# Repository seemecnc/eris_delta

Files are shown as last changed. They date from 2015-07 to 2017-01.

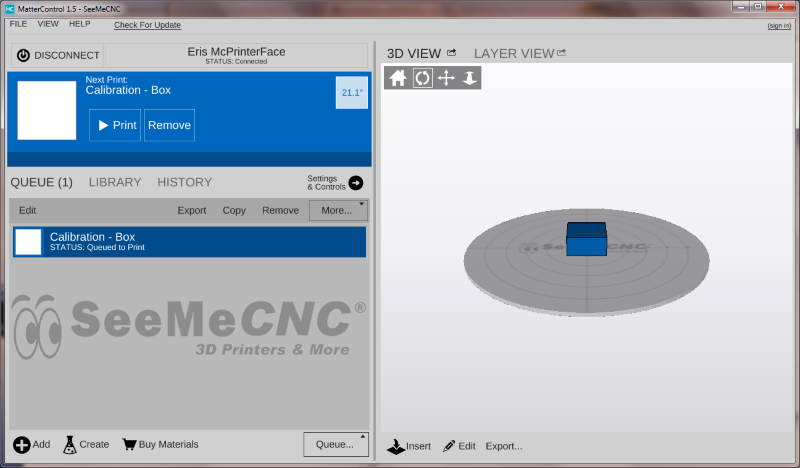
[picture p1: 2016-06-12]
User Guide/Images/mc running.png

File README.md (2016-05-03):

ERIS Delta 3D Printer
=====================

ERIS is an affordable desktop 3D printer built by SeeMeCNC.  We designed this machine to be fast, easy to use and much more affordable than any of our previous designs.  

3/2/16
DIR Repetier-Firmware-092.2-ERIS is workign on prototypes

3/3/16
DIR Repetier-Firmware-092.2-ERIS-ii2dh is modified 092 firmware from UltiMachine for accelerometer probing on new hotend PCB board

####

Case fan goes to fan port 2
Hotend fan goes to fan port 1

Red motor wire to right (opposite of the USB side of mini rabmo)

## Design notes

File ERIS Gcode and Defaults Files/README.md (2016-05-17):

This folder contains default settings files and calibration Gcode files.

ERIS_DEFAULTS.ini is the default slicing settings for MatterControl using
their Matterslice slicing engine

CALIBRATION.txt is the gcode script for calibrating using the accel probe
on the HE280 Hotend

LOAD_FILAMENT.txt is a gcode script to automatically load filament
in an eris delta.  MAKE SURE you only have the filament loaded to where you
can just start to see it coming out of the connector on the EZStruder NOT 
all the way up to the hotend!!!

UNLOAD_FILAMENT.txt is a gcode script to automatically unload filament
in an eris delta

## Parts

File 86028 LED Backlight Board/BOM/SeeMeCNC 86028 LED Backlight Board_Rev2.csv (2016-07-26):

LibRef | Comment | Description | Designator | Footprint | Quantity
ERJ-3EKF1001V | 1K | RES 0603 1K 100mW 1% | R19, R22, R25 | R0603 | 3
ERJ3EKF4701V | 4.7K | RES 0603 4.7K 100mW 1% | R26, R27 | R0603 | 2
GRM155R71C104KA88D | 100nF | CAP CER 0402 100nF 16V 10% X7R | C19 | C0402 | 1
CRCW0805180RJNEA | 180 | Resistor | R1, R2, R3, R4, R5, R6, R18, R21, R24 | R0805 | 9
APT3216VBC/D | APT3216VBC/D | LED BLUE CLEAR 1206 SMD | LED1, LED2, LED3, LED4 | LED1206 | 4
FIDUCIAL | FIDUCIAL | Fiducial | FID1, FID2 | FIDUCIAL-1X2 | 2
Header 4 | Header 4 | Header, 4-Pin | P1, P2 | HDR1X4 | 2
LTST-C19HE1WT | LTST-C19HE1WT | LED RGB DIFFUSED 0606 SMD | LED5 | LTST-C19HE1WT | 1
MMBT3904 | MMBT3904 |  | Q2, Q3, Q4 | SOT23-3 | 3
IC PCA9632 | PCA9632DP2 | IC LED DRIVER RGBA | U3 | IC TSSOP-10 | 1

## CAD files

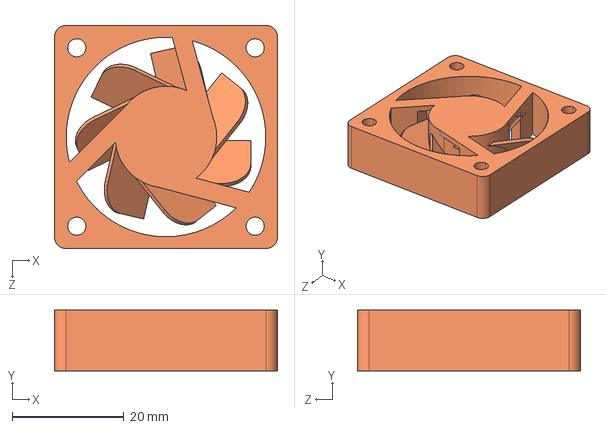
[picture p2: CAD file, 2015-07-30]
ErisRev1 CAD Source/Fan - 40mm X 40mm X 10mmT DC12V-015A - Copy.IGS
40.0 x 10.9 x 40.0 mm

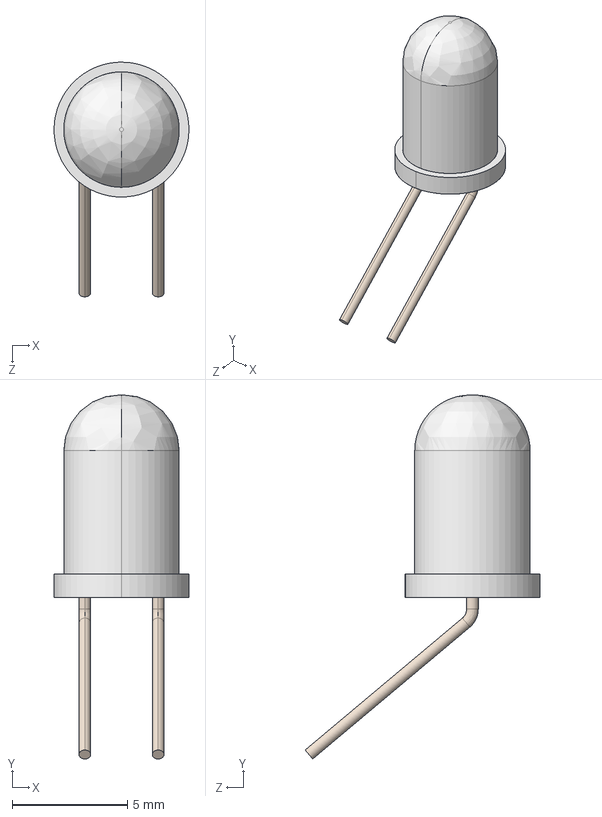
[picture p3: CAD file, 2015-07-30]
ErisRev1 CAD Source/LED - 5mm White.IGS
5.84 x 15.8 x 10.2 mm

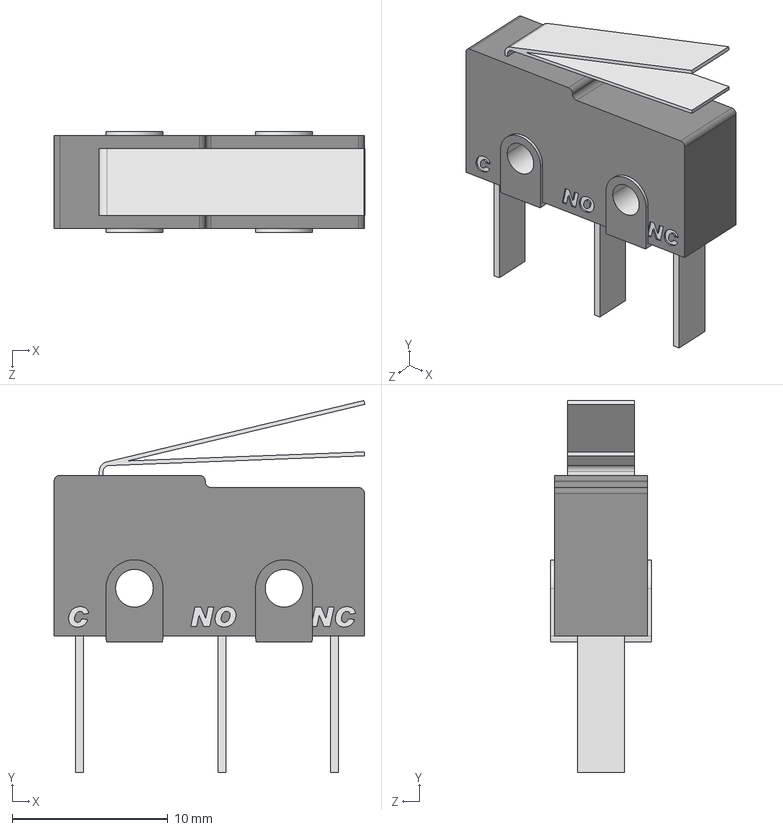
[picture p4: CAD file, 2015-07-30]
ErisRev1 CAD Source/Switch Micro Lever.IGS
19.9 x 23.9 x 6.48 mm

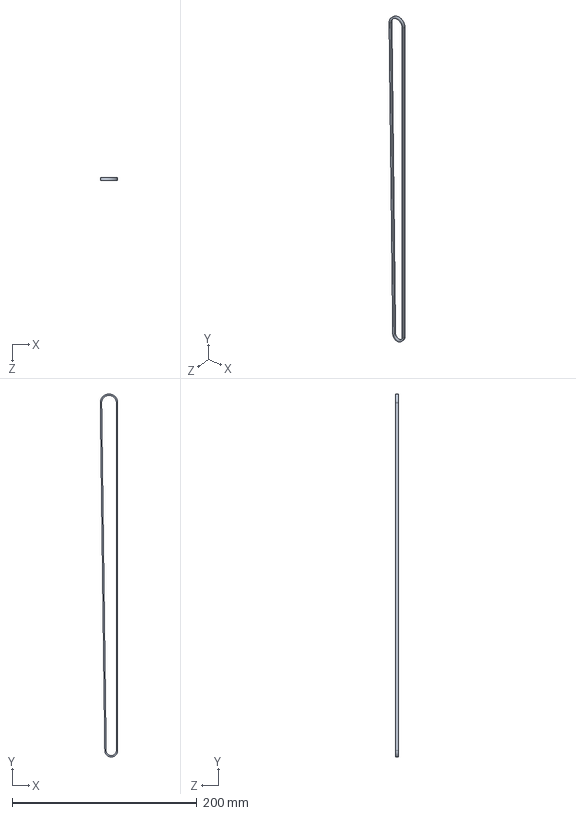
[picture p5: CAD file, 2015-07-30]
ErisRev1 CAD Source/GT2 Timing Belt 3mm.IGS
18.9 x 393.5 x 3.00 mm

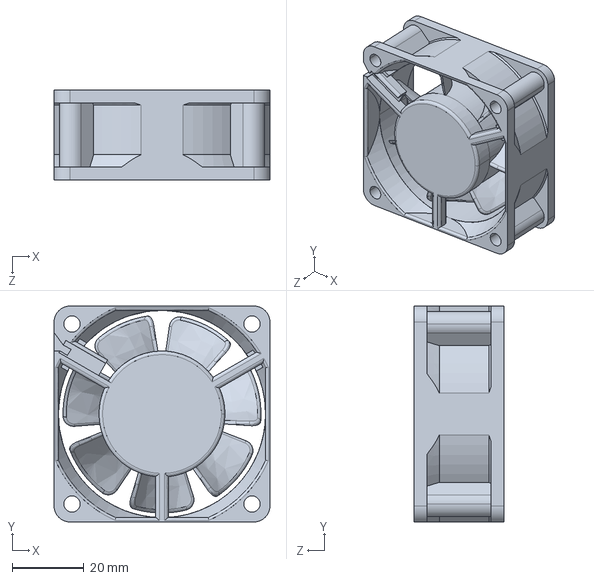
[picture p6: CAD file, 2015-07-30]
ErisRev1 CAD Source/Fan 60mm X 60mm X25mmT DC12V.IGS
60.0 x 60.0 x 25.0 mm

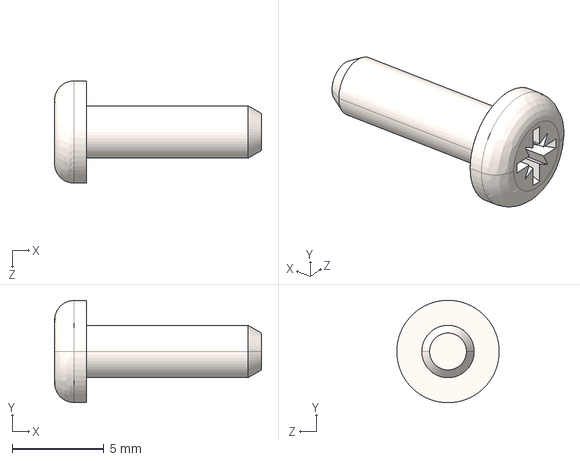
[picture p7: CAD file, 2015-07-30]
ErisRev1 CAD Source/No 4 x 0375L PANHTS SS Sheet Metal PANHTS 0.112-24-type II-B-0.375-N.IGS
11.3 x 5.56 x 5.56 mm

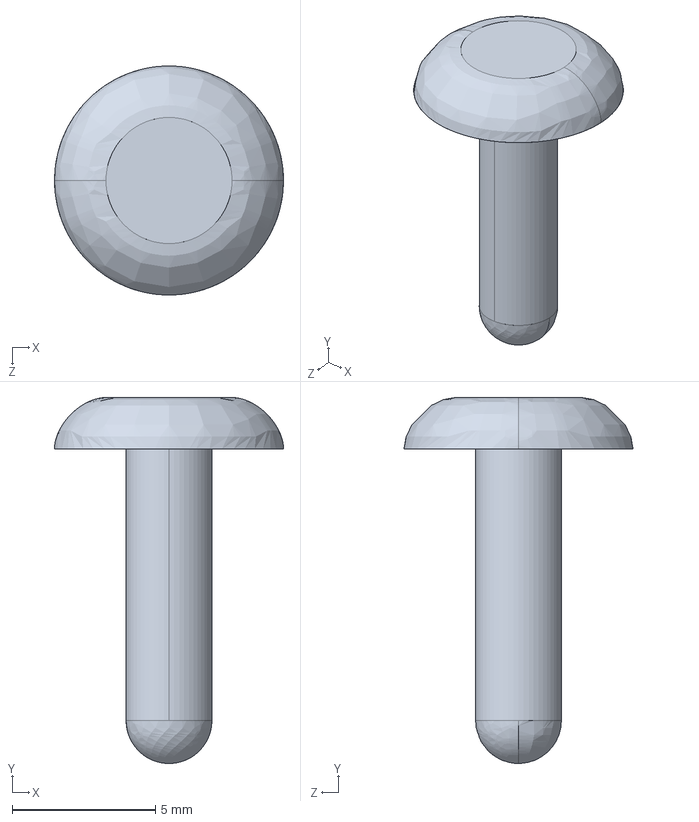
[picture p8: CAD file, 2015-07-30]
ErisRev1 CAD Source/Nylon Click-Lock Shank Rivet_Male.IGS
8.01 x 12.8 x 8.01 mm

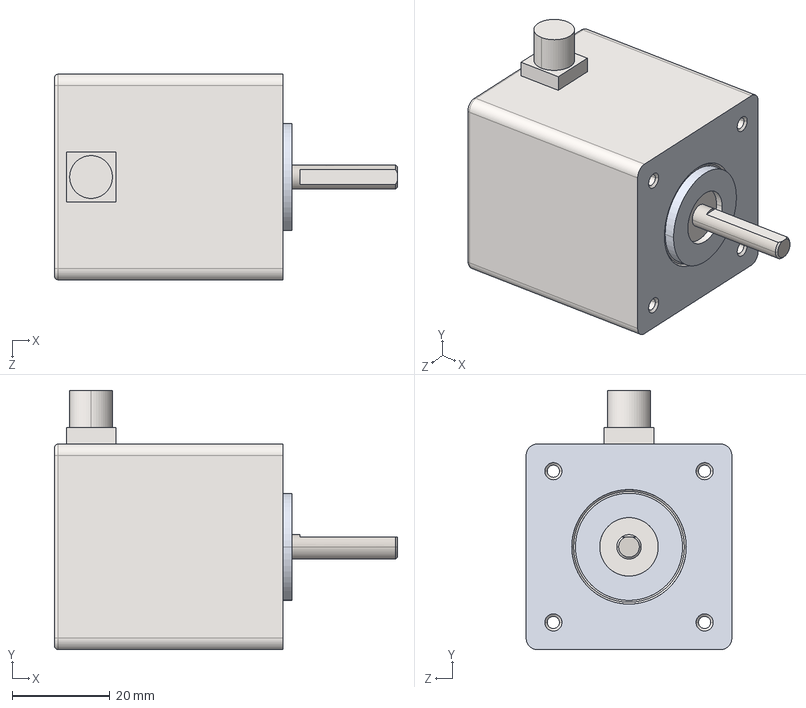
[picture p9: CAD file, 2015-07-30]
ErisRev1 CAD Source/NEMA 17 Stepper 5mmShaft wFlat 42BYGHW811P1.IGS
70.3 x 53.2 x 42.2 mm

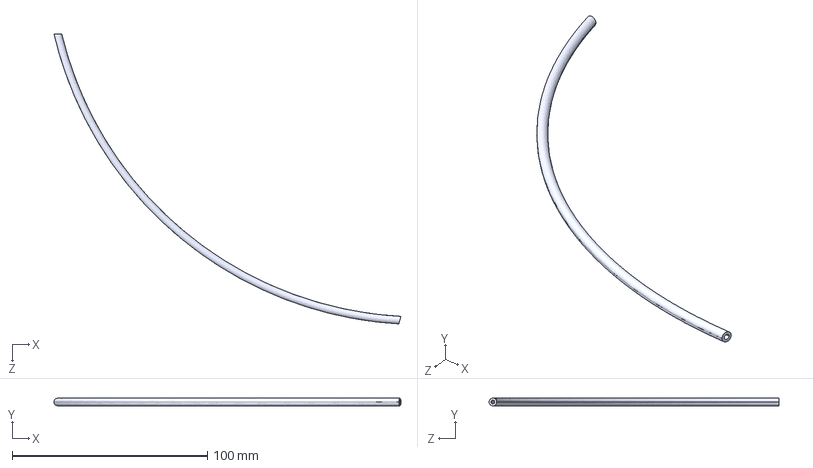
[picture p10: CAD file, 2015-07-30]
ErisRev1 CAD Source/Bowden Tube Model Only.IGS
177.5 x 4.00 x 148.2 mm

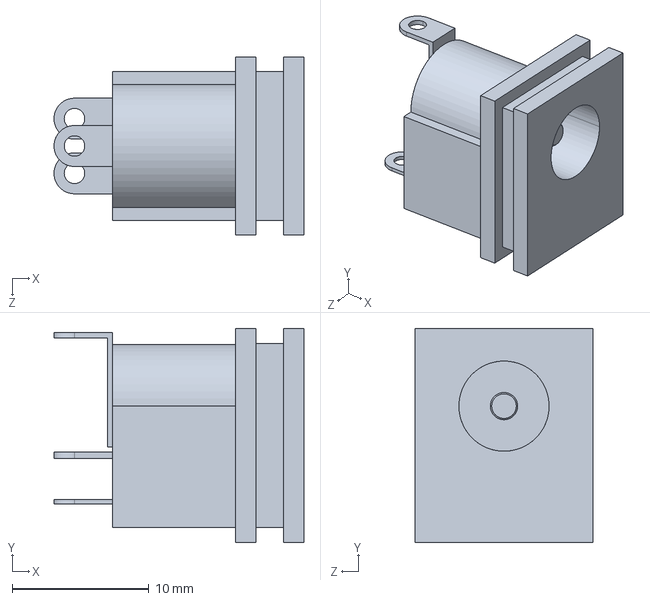
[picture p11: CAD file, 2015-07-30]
ErisRev1 CAD Source/Barrel Power Connector 2.0X6.6 PNL MNT.IGS
18.3 x 15.7 x 13.0 mm

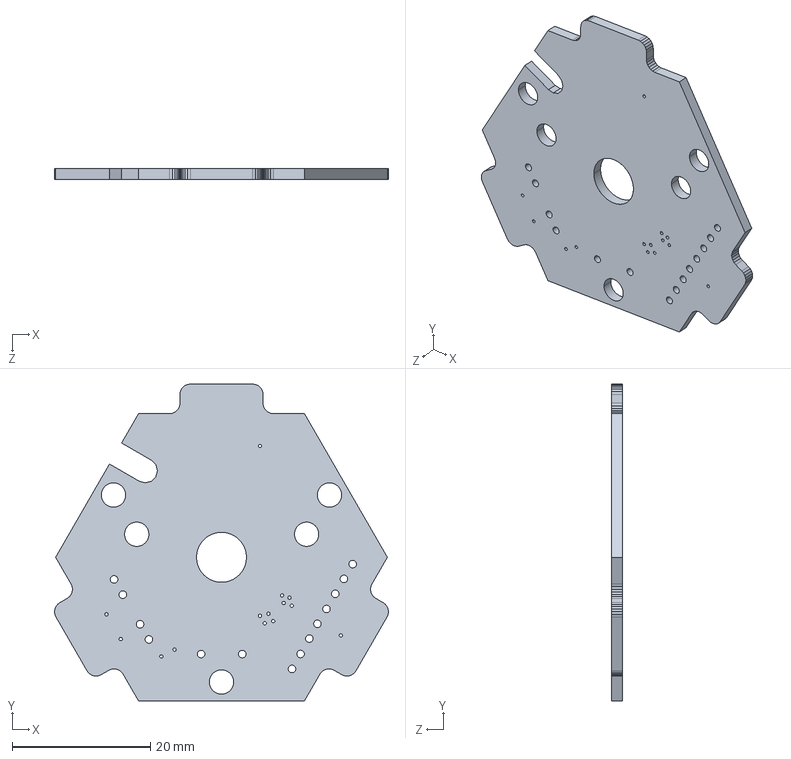
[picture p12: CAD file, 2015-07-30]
ErisRev1 CAD Source/Board.IGS
48.2 x 45.8 x 1.57 mm

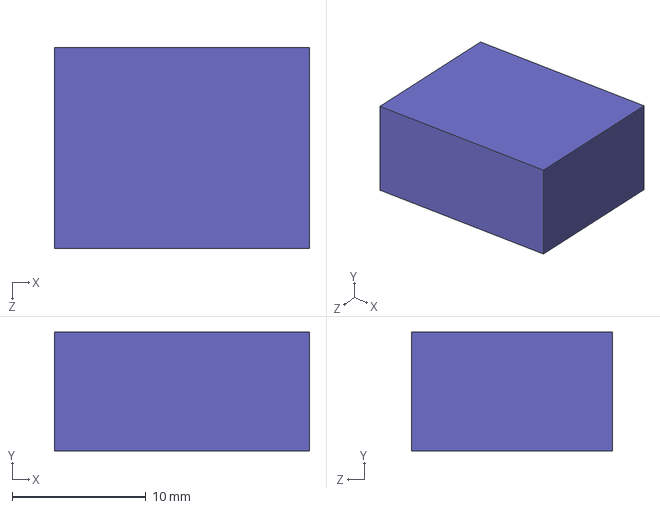
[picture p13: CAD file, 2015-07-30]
ErisRev1 CAD Source/10X2005X01W_51040681.IGS
19.0 x 8.89 x 15.0 mm

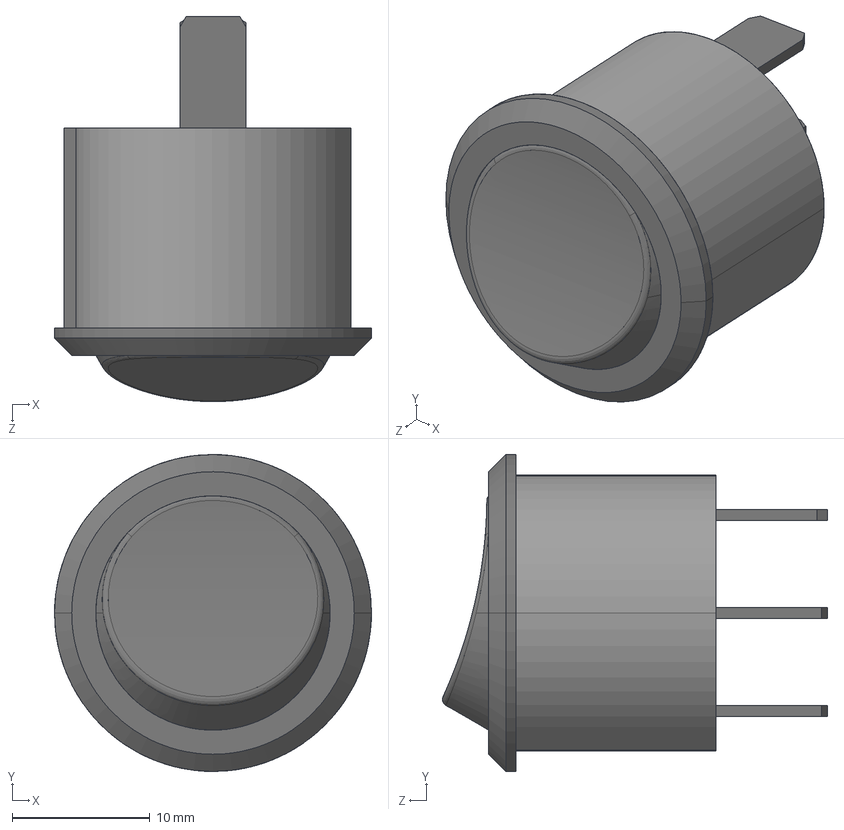
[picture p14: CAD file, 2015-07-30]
ErisRev1 CAD Source/Switch Rocker SPST SW-122.IGS
23.0 x 23.0 x 27.9 mm

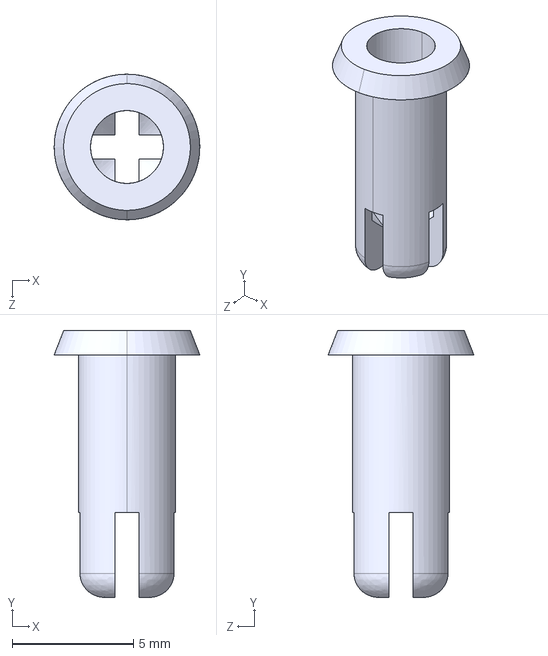
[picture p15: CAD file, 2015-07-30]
ErisRev1 CAD Source/Nylon Click-Lock Shank Rivet_Female.IGS
6.00 x 11.0 x 6.00 mm

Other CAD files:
ErisRev1 CAD Source/4-40 x 0375 SHCS.IGS
ErisRev1 CAD Source/filament 3mm.IGS
ErisRev1 CAD Source/No 4 x 0500L PANHT SS Sheet Metal Type II B.IGS
ErisRev1 CAD Source/No 4 x 0250L PANHTS SS Sheet Metal PANHTS 0.112-24-type II-B-0.25-N - Copy.IGS
ErisRev1 CAD Source/0250ID - 0625OD - 0196W.IGS
ErisRev1 CAD Source/16109 Foot_triangle base.IGS
ErisRev1 CAD Source/2512R055_RL2512FK070R06L.IGS
ErisRev1 CAD Source/39835 Timing Pulley 20T GT2-2.IGS
ErisRev1 CAD Source/6-32 x 1000L Phillip PH Screw Stainless.IGS
ErisRev1 CAD Source/70781 Drive Base Plate.IGS
ErisRev1 CAD Source/70782 Drive Roller.IGS
ErisRev1 CAD Source/70783 Arm.IGS
ErisRev1 CAD Source/70784 HEMA.IGS
ErisRev1 CAD Source/70785 Cover.IGS
ErisRev1 CAD Source/70788 1750 Bowden Adapter.IGS
ErisRev1 CAD Source/71566 Gear 15T 0950PD.IGS
ErisRev1 CAD Source/86001 Slide.IGS
ErisRev1 CAD Source/86002 Arm.IGS
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

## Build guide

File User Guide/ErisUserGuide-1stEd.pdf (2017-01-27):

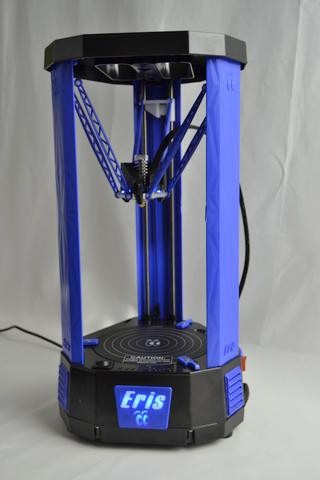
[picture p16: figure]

Eris® Delta 3D Printer Manual First Edition
v1.10 – January 27th, 2017 MatterControl v1.5
Copyright 2016 By Gene Buckle – geneb@deltasoft.com Licensed as Creative Commons, Attribution-ShareAlike 3.0
Disclaimer text provided by LulzBot. Official support is available through support@seemecnc.com As a new SeeMeCNC printer owner, you’ll also find a ton of great resources on the forums at forum (http://www.forum.seemecnc.com/) . (http://www.forum.seemecnc.com/) seemecnc (http://www.forum.seemecnc.com/) . (http://www.forum.seemecnc.com/)com (http://www.forum.seemecnc.com/)

### READ ME FIRST!

READ THIS MANUAL COMPLETELY BEFORE UNPACKING AND POWERING UP YOUR PRINTER!

### Hazards and Warnings

The SeeMeCNC Eris® Delta 3D printer has motorized and heated parts. When the printer is in operation always be aware of possible hazards.

### Electric Shock Hazard

Never open the electronics bay of the printer while the printer is powered on. Before removing the access door, always power down the printer and unplug the AC line cord.

### Burn Hazard

Never touch the extruder nozzle or heater block without first turning off the hot end and allowing it to completely cool down. The hot end can take up to twenty minutes to completely cool. Also, never touch recently extruded plastic. The plastic can stick to your skin and cause burns. Also before of the heated bed which can reach high temperatures capable of causing burns.

### Fire Hazard

Never place flammable materials or liquids on or near the printer when powered on or in operation. Liquid acetone and vapors are extremely flammable.

### Pinch Hazard

When the printer is in operation, take care to never put your fingers in the moving parts, including the belts, pulleys or gears. Also, tie back long hair or clothing that can get caught in the moving parts of the printer.

### Static Charge

Make sure to ground yourself before touching the printer, especially the electronics. Electrostatic charges can damage electronic components. To ground yourself, touch a grounded source.

### Age Warning

For users under the age of 18, adult supervision is recommended. Beware of choking hazards around small children.

## Table of Contents

## 1 – Unboxing your new Eris® Delta 3D Printer

If you're one of the rare people that downloaded the manual BEFORE opening your new Eris®, SeeMeCNC has a treat for you!
We've produced a short little video that shows how to unpack your new Eris® as well as how to load filament for the firs time!

# Eris® Unboxing and Setup Video (https://www.youtube.com/watch?v=lwgVCTLGT_E)

## 2 – Installing MatterControl

MatterControl is the control program that you'll be using with your new Eris® printer. MatterControl is known as a combination host and “slicer”. It's “host” feature allow you to control the Eris® directly – moving the axes, heating the hot end, etc. The “slicer” feature is what converts a 3D model into a form suitable for printing. We'll cover that shortly.

You can download MatterControl by going to the SeeMeCNC website – http://seemecnc.com/pages/downloads. Scroll down to the “Software” heading and you'll see the links for MatterControl. Download the version for your platform and install it.
Note that the MacOS version is functionally identical to the Windows version, so I'll only be showing examples from Windows – the same procedures should apply to both versions.

You'll also want to download the Eris® Default Files from the Eris® page on the SeeMeCNC website: https://www.seemecnc.com/collections/3d-printers/products/eris-desktop-3d-printer. (https://www.seemecnc.com/collections/3d-printers/products/eris-desktop-3d-printer) Look for the link marked “DOWNLOAD ERIS SETTINGS HERE”. Unpack the files so they're ready to use when you need them.

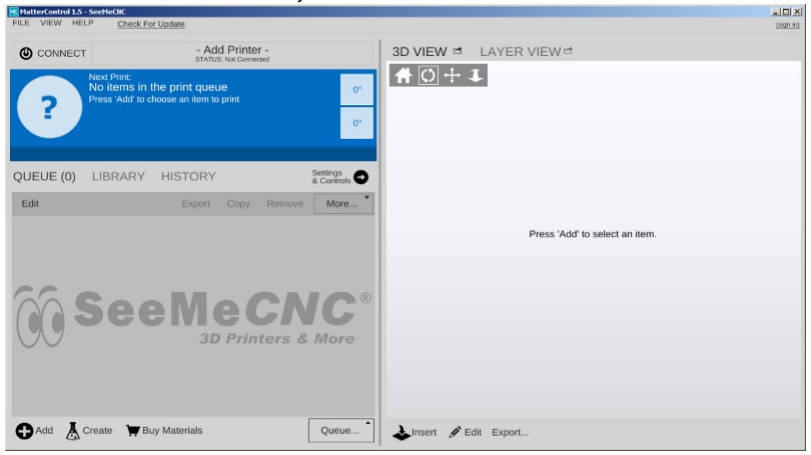
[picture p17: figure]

Start MatterControl. Below you'll see what the basic MatterControl interface looks like.

Your first step will be to configure MatterControl to use the Eris®. Simply click the “Add Printer” button that's located at the top of the left MatterControl pane.

When you click on the Add Printer button, you'll be presented with the dialog you see to the right. Click in the Printer Name field and enter the name of your new printer. Next, click the Select Model button and pick “Eris”.

Click the Save & Continue button to move on to the next step.

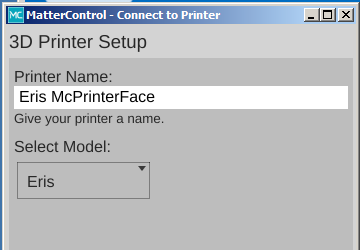
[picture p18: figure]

Next, you'll be presented with the option to install

the communication driver that MatterControl needs to talk to the Eris®. If you've used a RAMBo or Mini-RAMBo based 3D printer on your computer before, you can skip this step. Otherwise, click the Install Driver button to have MatterControl install the driver for you. MatterControl will run a driver installer that will likely ask you for permission to continue. Please grant it and a dialog similar to the one below will appear. Click on the Install button to allow the driver to install.

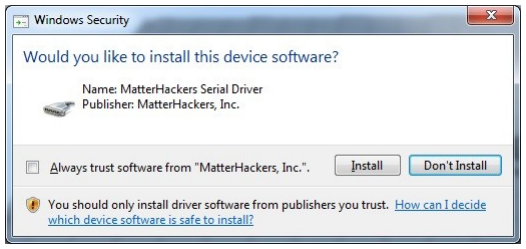
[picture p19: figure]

Once the installer finishes, MatterControl will attempt to automatically configure the connection. Please disconnect the Eris® and click the Continue button.

Once you click on Connect, the following dialog should appear:

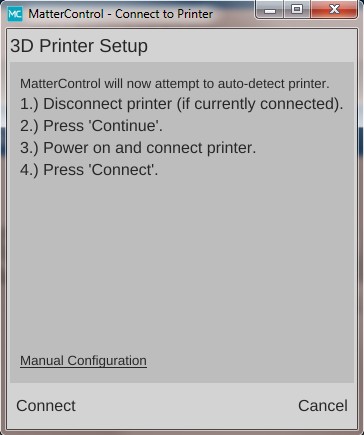
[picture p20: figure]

Congrats! You're all done. Click on the Done button to continue.

The configuration process automatically loads a test object that you can print. Let's take a few minutes to go over the various features of the MatterControl interface.
The MatterControl interface
is split into two halves. The left
half is where you can load objects
or G-code to print, start prints, and manually control the printer.
1. This is the print queue display. If nothing is queued up, you'll see the message, “No items in the print queue”. To add an item, click the “Add” button (#13). We'll cover this in detail later. Note that you can only select STL or GCODE files.
2. This is the temperature display. The figure displayed shows the current nozzle temperature. If you ever install a heated bed on your Eris®, a second box will appear that will show the bed
temperature. Both values are shown in degrees Celsius.
3. Queue Count. This shows the
number of objects currently in the
print queue.

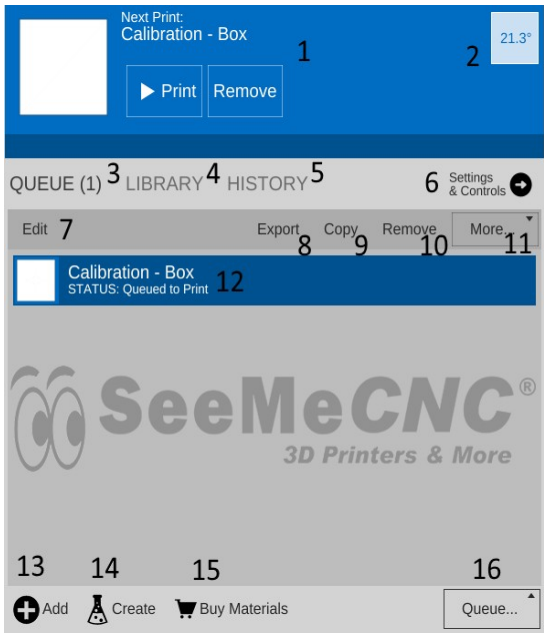
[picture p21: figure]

4. Library – This is a list of items that you've stored in your object “library”. We'll cover this one in detail later.
5. Print History. This will show you what you've printed in the past along with statistics about each print.
6. Settings & Controls – this is where you can edit your slicer & printer settings as well as manually control your Eris®
7. The Edit button will allow you to choose which items in the print queue will be available for printing.
8. The Export button will allow you to export the currently select item as an STL, AMF, or GCODE file. You can use this to save GCODE if you want to share your sliced object with another Eris® user.
9. The Copy button will make copies of the currently selected item in the print queue.
10. The Remove button will remove the currently selected item in the print queue.

11. The More drop-down will allow you to send the currently selected item to another device, or to the print Library.
12. Items currently in your Queue.
13. The Add button will allow you to add objects or G-code files to the print queue.
14. The Create button displays a list of available plug-ins that are used to create printable objects right inside of MatterControl.
15. The Buy Materials button will open your web browser and point it to the SeeMeCNC store.
16. The Queue button opens a menu list that will allow you to export the current file and perform other operations on the print queue.
The right half of the MatterControl interface is taken up by a 3D view of your build platform and what objects are currently loaded and ready to print.
1. The 3D and Layer view controls allow you to switch between the 3D view (shown) and the Layer view. The layer view shows
you the path the print head will
take as your part is printed. The
layer view won't display anything until the part you want to print has been “sliced”.
2. View manipulation controls – Rotate, Pan, and Zoom. By
default, the 3D view will show a rotating display of the part. You can stop the rotation by clicking anywhere in the 3D view window.
3. The object currently ready to print.
4. This is a representation of the print bed on your Eris®. As long as your object fits within the
circle, you can print it!

5 & 6 The Insert and Edit buttons allow you to add and manipulate multiple objects to the current print job. We'll cover this in depth later as well.
7. The Export button allows you to save the current state of the build plate in a few different file formats.

## 3 – Calibrating the Eris®

Before you can start using your new Eris®, we'll need to calibrate it first. This is really easy to do!
Click on the Settings & Controls button and then click on the Options button.

Once you're on the Options page, click on the Show Terminal button to open up the serial console.

Before you proceed to the next step, make sure that the nozzle on the hot end is free from any filament or other debris. A clean nozzle will ensure a clean “hit” as the calibration routine probes the bed surface. You also want to make sure that you've got the hot end cold – the calibration process will not work reliably if the hot end heater is active.

Click in the input field
as shown and enter G29
and press the enter key.
This will run the calibration process on your Eris®!
This probing process
works out a few basic
parameters about your
Eris® and is considered a
“basic” calibration.

In order to obtain the best calibration possible for your Eris®, you should also use the online calibration wizard that SeeMeCNC has created. This tool is very easy to use and includes very detailed instructions on how to use it!
The calibration wizard can be found here:

https://www.seemecnc.com/pages/delta-calibration-wizard

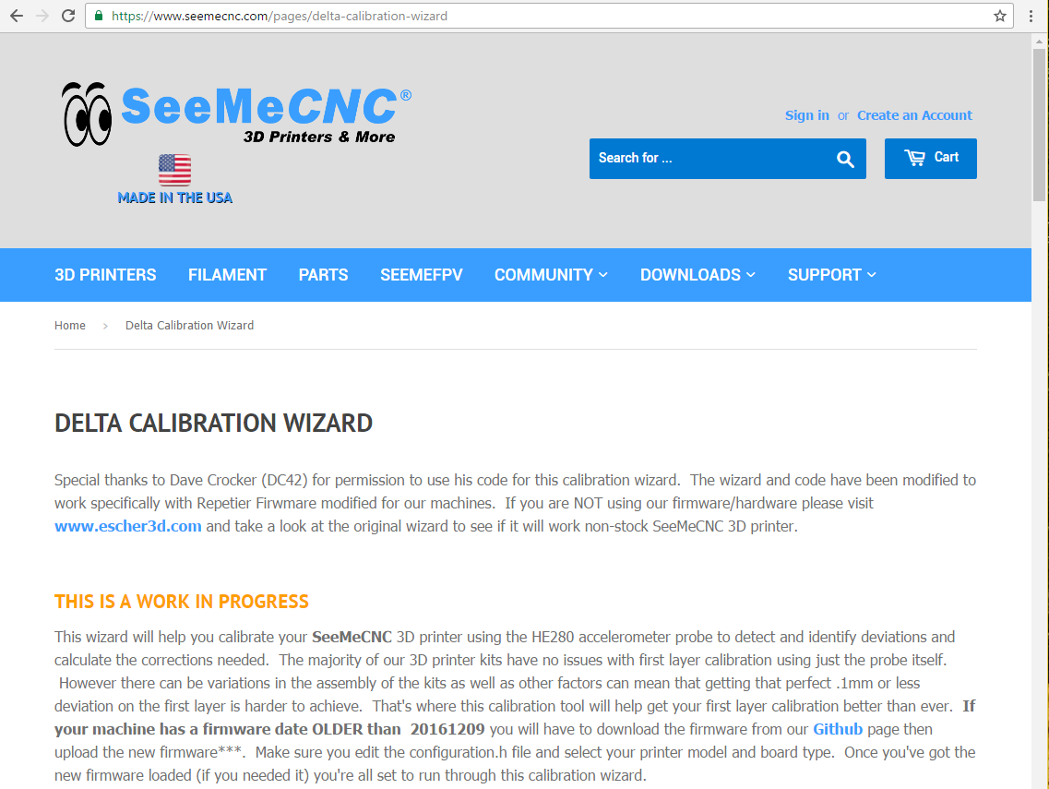
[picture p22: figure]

## 4 – Loading and Unloading Filament

Loading new filament into your Eris® is a very straightforward task. First, you'll need to feed new filament into the filament guide tube on the Eris® as shown below:

Open the filament tensioner by compressing it between your thumb and forefinger, then feed the filament into the EZStruder.

Feed only enough filament to exit about 1” past the PTC fitting on the outfeed side of the EZStruder as shown below.

Into the guide tube...

...to the EZStruder...

Compressing the filament tensioner.

1" feed through.

In MatterControl, click the LOAD FILAMENT item in the queue to make it the active job and click Print.
The Eris® will begin to heat
the hot end up to operating
temperature and it will then finish

feeding filament in and prime the hot
end.
You can tell the Eris® hot end is active by looking for the red LED on the effector PCB as shown below.

Unloading filament is just as easy – go to the queue and choose the Unload Filament item and hit Print! The Eris® will bring the hot end up to operating temperature and then rapidly back the filament out of the system.

## 5 – First Print!

Since MatterHackers was kind enough to supply us with a small calibration cube, let's make that the first print!

Before your first print, make sure that the build surface is clean and free from finger prints. The oils in your fingers can cause prints to not stick sometimes. The easiest way to clean the Eris® build surface is with either soap & water (rinse well!) or with a small alcohol wipe – these are perfect for getting finger marks cleaned off!

Because we've already loaded the Eris® defaults, all you'll need to do is click on the object (Calibration – Box) and then click Print to being the print job.

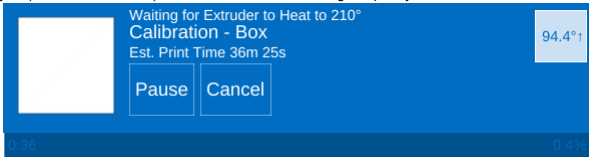
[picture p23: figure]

With the print job started, you'll notice that the hot end temperature is increasing and there's a tiny up-arrow indicating that the hot end is active and is heating. When the set temperature is reached, the little arrow will go away.
The display will also give you an estimate of the time it will take for the print to finish. Sometimes the estimate is a ball park, sometimes it's a national park.

Congratulations on the first print from your new Eris®!

## 6 – MatterControl Basics: Slicing

MatterControl is a very complete 3D printing package and it's got a LOT of options. Some people can find this intimidating, but I assure you – there's nothing to be worried about! MatterControl is an integrated host application. This means that it provides everything needed to control the Eris® and to prepare models for printing. The task of preparing a model for printing is called “slicing”. It's a very descriptive term for what is actually happening. In order to print a 3D model, it needs to be converted from a solid object into a series of very thin layers that are in turn converted into G-code (special instructions that tell the printer how to move). For example, if your print layer height is 0.2mm, the slicing tool is going to “slice” your model into a number of layers – basically the model height divided by 0.2mm. For a tall part, this can mean a LOT of layers!
MatterControl provides three slicers for your use. MatterSlice, CuraEngine, and Slic3r. This guide will only cover the specifics of MatterSlice, but don't let that stop you from experimenting with and using the other slicers! I'll show you how to change the slicing engine later on in this guide.
The final task of the slicer is to translate the sliced layers of model into something called G-code. G-code is a simple control language that's used to position the print head and tell the extruder how much plastic to deliver and at what rate. Going into the details of G-code is beyond the scope of this guide, but if you'd like to learn more you can check out the following resources: http://en.wikipidia.org/wiki/G-code and http://reprap.org/wiki/G-code.
For the most part, you'll never directly interact with G-code, but it's nice to know what's going on behind the curtain!

I want you to click on the Settings & Controls button to bring up the Settings, Controls, and Options pane.

Click on the SETTINGS link to make sure your display follows (by and large) what you see below.

The first thing I want you to do is click on the Show Help check box that's highlighted by the arrow in the image above. This will turn on verbose descriptions of each one of the parameters available in the Settings page.
I'm going to only cover the “Simple” configuration settings for right now. There's a LOT that goes on to configuring your slicer and the Simple configuration setting allows many of those to be hidden until you're more comfortable with how your printer works.
Layer Height – This parameter tells the slicing engine how thin to make the layers when it slices up the model as I described earlier. A good default layer height is 0.2 or 0.25mm. The lowest practical layer height with a 0.5mm nozzle is 0.1mm. You can go lower than that, but it requires a smaller nozzle diameter. You can also got a lot thicker, but that requires a larger nozzle. If you change the Quality from Standard to Coarse or Fine, you'll notice how the layer height changes.

Here's what the Coarse, Standard, and Fine layer heights look like when printing the little test cube.

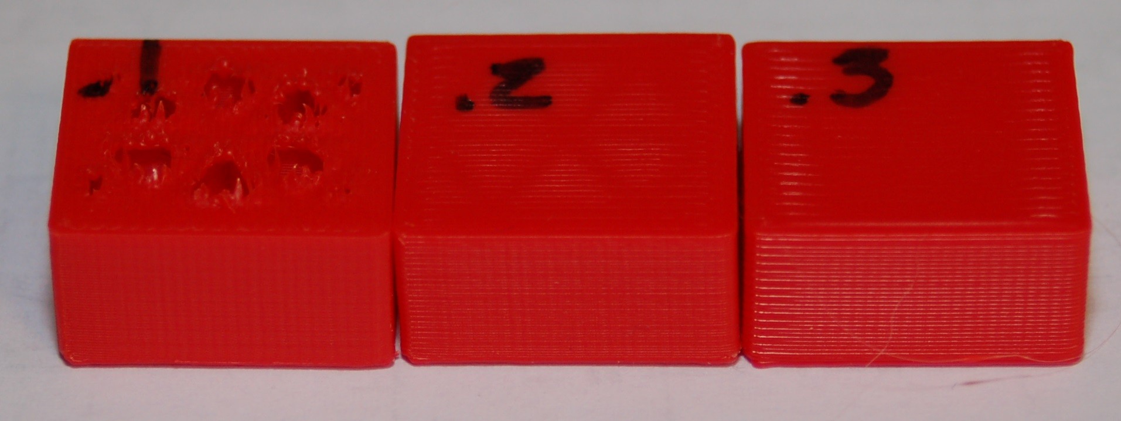
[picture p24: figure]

Starting from left to right, the layer heights are 0.1mm, 0.2mm and 0.3mm. You'll notice that the top layer on the 0.1mm print is kind of ratty and torn up. This is because the number of top layers is set to 3. This is perfectly ok with thicker layer heights, but it should have been set to at least 5 for the 0.1mm layer height that the Fine setting uses. You'll learn how to tweak that in a little bit.
You can see how the smoothness of the sides decrease as the layer thickness increases. If you want to print something really quick, you could go up to a 0.35mm layer height. I wouldn't recommend anything over 0.40mm if you're using a 0.5mm nozzle however. Fill Density – This parameter controls how solid your printed part is. The number is a percentage, from 0 (totally hollow) to 1 (totally solid). The default fill density (also known as “infill”) is 0.2 or 20%. The image below shows what that looks like inside our little test cube. You can tweak the infill to get a more

robust or a lighter part. For most prints, 20% is a
good infill value.
The Fill Density option also allows you to choose one of three preset values. Light sets the infill to 10%, Standard to 30%, and Heavy to 90%.
Later on I'll show you how to change to a different infill pattern. The one shown on the right is the Triangle pattern.

Support Material – Support material is used when the part you're printing has free-standing features (like the chin on a bust) or another feature that requires it to be physically supported during the printing process. When you check the Support Material box, the slicer will automatically design support for the part that's currently (or will be) loaded.
Create Raft – A raft is essentially what it says, a “raft” of material that your part will print on top of. Rafts are most often used when printing a part that is having bed adhesion problems due to its geometry. For example, if you're printing a part that sits on small feet, a raft would come in handy if the initial layers of the feet don't stick very well.
In the image below, you'll see an example of both support material and a raft.

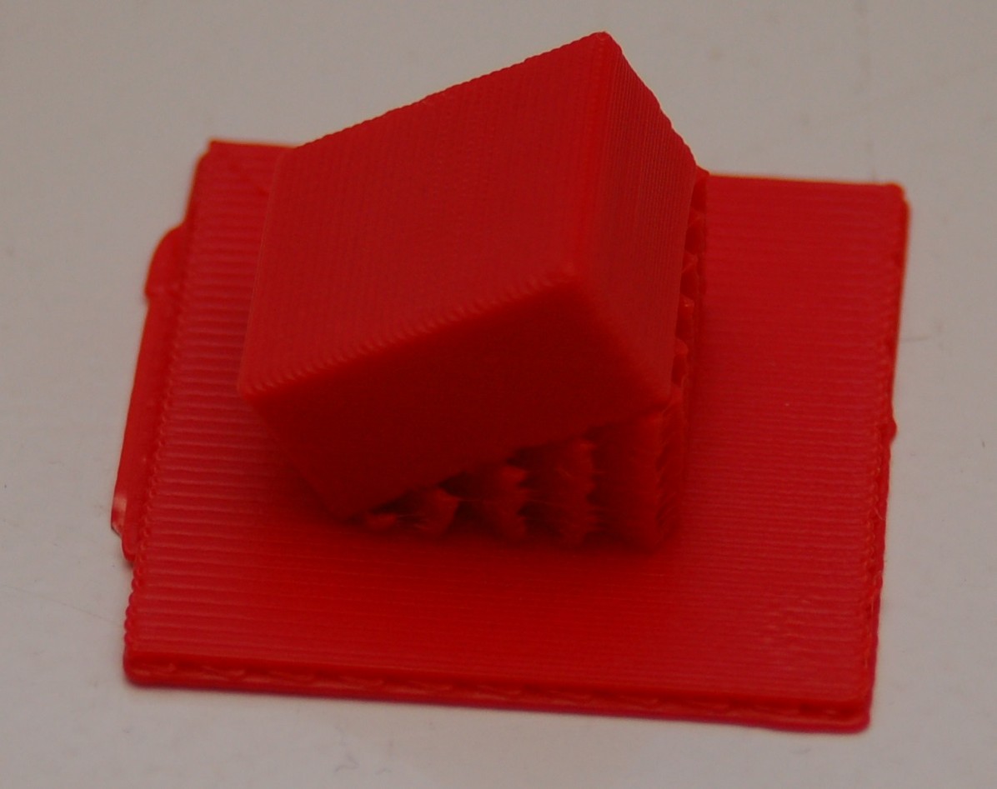
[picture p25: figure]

I took the little test cube and through a little manipulation, printed it tilted at 30 degrees. I took this opportunity to also demonstrate what a raft looks like. This one is exaggerated in its size, but gives a great example of what a typical raft will look like.

The image to the right should give you a

pretty good idea of what the part looks like from the side. You can easily see the support material as well as the layer lines that will be at a 30 degree angle when the little cube is laid flat.
Support material is generated in such a way that there is just enough of it there to handle the actual print layer that it will be supporting. In my example, the support material has a 2.5mm spacing between the walls of support material and it uses an infill angle of 45 degrees.

The printed part will usually separate from the support material fairly easily – however, some material will be left behind if you're using a raft. Cleaning up the left over support material is a simple and straightforward task.

Here's what you end up with after removing the support material from your part. As you can see, there's still a little clean up to to be done to the printed cube (on the left). A quick hit with some 220 grit sandpaper will knock the rough edges of the support material down.

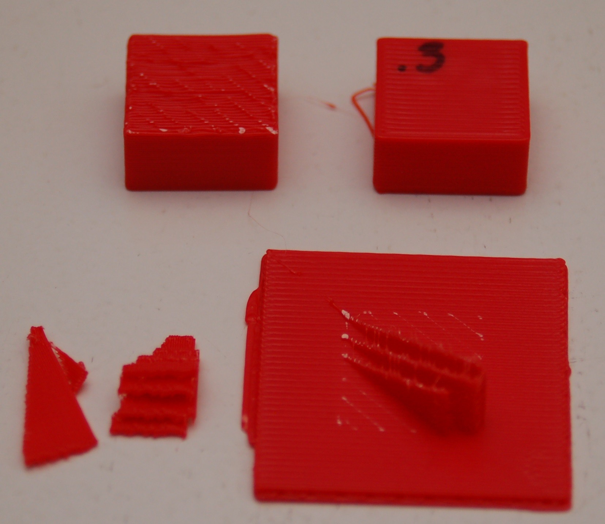
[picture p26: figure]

That's pretty much all there is to the Simple settings level. Next, let's dig into the Standard setting!

Click on the Simple setting drop down and pick Standard. Your MatterControl settings screen should change to something resembling the image below.

Quite a number of new configuration options are accessible under the Standard settings level. The first set of options we'll tackle live under the General heading.
Layers/Surface – This setting page allows you tweak the layer height just as before when in Simple mode, but now adds the First Layer Height and Outer Surface settings.
The default First Layer Height is 0.3mm. This will create a good first layer when using the 0.5mm that comes with your Eris®. The thicker layer provides more surface area for the follow on layers to adhere to.
The Outer Surface setting allows you to specify how thick the “skin” of your printed part will be. The default setting will result in a skin thickness that is roughly 1mm. This translates as two “perimeters” in the part – the hot end will travel around the perimeter of the part twice, as it prints the outer surface of the part.
On the left is an example of what two perimeters look like.

When the cube is being printed, the #2 perimeter is printed first and then the #1 perimeter. (The order is configurable.)
I

In the image below you can see what those perimeters actually look like on the example cube I printed.

Infill - The Standard level adds Infill Type in addition to the Fill Density figure we covered before. The infill types available are Triangles, Concentric, Grid, and Lines. Examples are shown below.

The Lines infill pattern differ from the others in that the line orientation is alternated every other layer. All the examples show a 20% infill density.
You're probably wondering which infill pattern is “best”. I wish I could go into that, but I've been unable to locate any studies that cover the topic in any depth. If I were asked to provide a recommendation for a good structural pattern I would probably pick the Triangles option. It offers a good internal structure for most infill densities that I've used it with.
Skirt and Raft – This is a new option that appears with the Standard and Advanced setting levels. The Skirt option is used one of two ways. First, it can be used to “prime” the hot end with filament before the actual part itself begins to print. You may notice that your hot end may “drool” filament while the bed is heating up and the hot end has already reached temperature. This is perfectly normal. However, without some kind of priming action, early features of your part may not print properly. The Skirt solves this. Secondly, the Skirt can become a “brim” if the Distance from Object setting is set to zero. What this does is make sure that the skirt is physically connects to the part, becoming a brim.
Triangles | Concentric | Grid | Lines #1 | Lines #2

This can be handy when you're printing a small part and you're having bed adhesion issues and you don't want to have to use a raft. Later on in the Advanced settings section, you'll see more options on how you can tweak the Skirt and Brim settings.
Support Material – With the Standard and Advanced setting levels, you get more control over how the support material for your part is generated.
The new option here is called Support Type and allows you to choose a LINES or GRID pattern for the support material. When I printed the support example, I used the LINES mode as that is the default for the Simple settings mode. Looking down on it from above, this is what the LINES support material pattern looked like for that print.
This shows the second layer of the print. The lines will continue to stack upon one another for the entirety of the support structure.
The GRID pattern (on the right) uses the same
spacing as the LINES option, but is designed to provide
more support where it may help to provide a better end result.
Interface Layers will allow you to specify where to place a solid support layer when the standard support structure isn't enough for the part you're printing.
Normally MatterSlice will only generate support for those elements that can be supported with the support structure starting from the bed surface. If you check Support Everywhere, MatterSlice will add support where ever it's needed.
Standard also exposes a new support tuning category called Support Options. Here you can adjust the Pattern Spacing and Support Percent. Pattern Spacing controls the distance between support material lines. A wider spacing may create support that's easier to remove, but may not support as well as a narrower spacing.
Support Percent controls when support will be generated. Most slicing software will allow you to define an overhang angle that must be reached before support will be generated. MatterSlice looks at it a bit differently. Support Percent basically instructs MatterSlice that; “If the next layer path covers n% or less, you should generate support underneath it.”
Here's a visual example that will help you understand what's
going on.

The layer stack on the right is angled at 45 degrees. You'll notice
that each layer only overlays the layer below it by around 25%. With a Support Percent value set to 50%, this would cause support to be generated.
Extruders/Support Material Extruder tells the slicer which extruder to use when generating support. This option is only really meaningful if you're using two extruders and have one dedicated to a special filament meant for support structures (such as PVA).

The next new category exposed under General by the Standard setting is called Filament. Under the Standard setting, the only option is Filament. This allows you to set three parameters that deal directly with the material you're currently using to print with. Diameter – This is the diameter of the filament you're using. The more accurate this figure is, the better the quality of your prints. This is because the slicer uses the filament diameter to help calculate the optimum flow rate for the extruder during the print.
In order to get an accurate filament diameter, spool off a meter or so of filament and check it in 10 spots along the length of the material. Record the measurements using a digital micrometer and average the results. That average should go into the Diameter field. Extruder Temperature – This figure determines the target temperature of the hot end for the material you're printing with. A typical heat range for ABS is 220 to 240C and 190 to 220C for PLA. Other materials will have their own recommended temperature ranges. The maximum operating temperature for the Eris® hot end is 240C.
Extruder Wipe Temperature – this parameter is only applicable to printers that have a special wipe mechanism and shouldn't be used with the Eris®.
Bed Temperature – Like the Extruder Temperature the bed temperature is material-dependent. For ABS, a typical heated bed temperature range is between 80 and 100C. For PLA a heated bed isn't required. Note that the Bed Temperature parameter may not appear unless you've indicated to MatterControl that you've got a heated bed installed.
The Retraction group includes Length on Move, Speed, Z Lift, and Wipe After Retract. These items control how the slicer deals with filament retraction. Retraction is used to help minimize or eliminate “stringing” during a print.
Length on Move specifies the distance the filament will be retracted from the hot end during a rapid or “non-printing” movement takes place.
Speed controls the rate at which the filament is retracted and re-extruded.
Z Lift controls the height at which the hot end is lifted after a retract, but before a rapid move is started. This helps to eliminate stringing.
Wipe After Retract – if checked, will cause the nozzle to retrace up to 10mm of the last move after retracting. This is also an anti-stringing measure.
Each filament can have different heating requirements, even within the same type and color! For example, it's not unusual to have two rolls of identical material require different hot end settings. Bed temperatures tend to be less variable. When you're working with a new roll of filament, I recommend printing a test object or two in order to find out what the best temperature setting works best with that material. Note the settings on the spool label, or add your own. This presents a nice opportunity to explain another feature of MatterControl – material profiles! You'll notice a little pencil icon next to the material drop down

Click on that to open the preset manager. The Material Presets list
shows you what pre-configured

material settings you've got available
to you. When you get a new roll of filament in, you can easily keep track of its settings by using this system. Click on the Add button and we'll create your first custom material! When you click on the Add
button, you'll be presented with a screen that looks something like the one shown below. The Edit Preset: field is where you can name this new material configuration. In this
example, I've named it after the
vendor, the material color and the
date I purchased the material. Since this is the first time I've used this material, the only thing I know for sure is what the average filament diameter is. To enter that, I picked Filament from the Select Category drop down, then from the Select Group drop down, Filament was chosen again and finally Diameter was selected from the Select Setting drop down. I entered the diameter that I calculated using the process outlined earlier.
The default for the Eris® to print PLA is 210C, so I'll set that as well in this profile. It can always be changed later if it's found to be too hot or too cold.

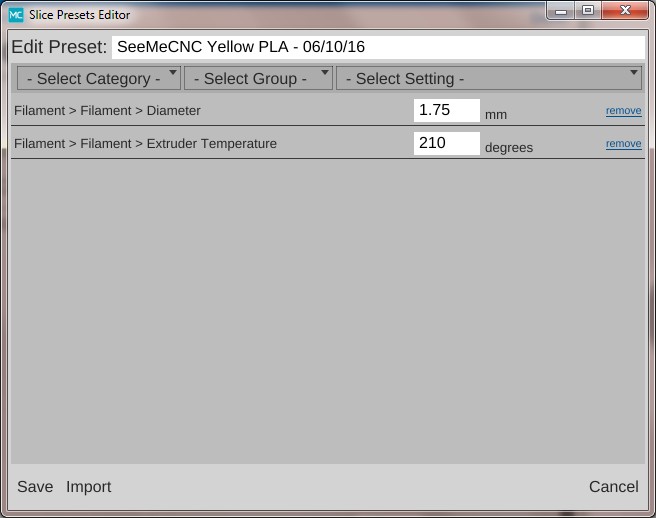
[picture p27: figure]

Click on the Save button to commit your changes. Congrats, you've added your first custom material profile!
After you've saved your new profile, it will
appear as the currently selected material as shown
to the right.
Now say you've printed a test cube and have decided that the print might look better if you bumped up the temperature 2 degrees. This is a simple change to make. If you hover your mouse over the Extruder Temperature option, you'll see

that the foreground is covered by an EDIT PRESET button as shown below.

Clicking on the button will open up the materials editor and allow you to change the temperature. It's as simple as that!
Before we move on to the next topic, I wanted to cover one more item – the QUALITY presets. I'm not going to go in depth on this one except to note that both the QUALITY and MATERIAL presets can store identical settings. They're split into two categories in order to make it easier for you to group common settings together. You will typically store things that directly affect the print quality of your model in the QUALITY presets. Things like layer height, print speed, etc. MATERIAL presets should only contain those settings that directly deal with the material you're using to print the current object with. You'll find that both the QUALITY and MATERIAL presets contain more options than I've covered here. Those new options are exposed by choosing the Advanced settings level. I'll be reviewing those with you later on. We've covered both the Simple and Standard settings for the slicing engine. Advanced is something I'll cover later, so let's move on to the CONTROLS section.
The CONTROLS page is where you can manually control your Eris® 3D printer. You can heat the hot end or bed, as well as manually position the effector platform and extrude plastic.

The Temperature pane contains everything you need to manually control the temperatures for both the hot end and the heated bed. MatterControl provides room for up to three temperature presets. You can edit them by clicking the pencil icon next to the Extruder Temperature label. Creating a temperature preset will create a new button that will be aligned with the pre-existing OFF and PRESET buttons. You can also enter in a temperature and heat to that value by clicking on the SET button that will appear as soon as you begin typing.

The Movement Controls pane contains controls that will allow you to manually position the Eris®'s effector platform.

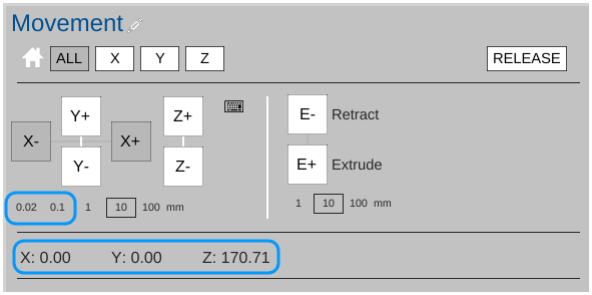
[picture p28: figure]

The row of buttons to the right of the little house icon control “homing” of the movement axes in the Eris®. Because the Eris® is a delta configuration printer, the only buttons active are the ALL and Z buttons – they perform the same action. Connect your printer if you haven't already and click on one of them to see what I mean. The printer will home itself and await further instructions. (Good robot! Have a Scooby Snack!) The RELEASE button will tell the Eris® to power down the stepper motors so that the motion axes and extruder can be moved by hand. This is handy when you want to load new filament into the printer without having to turn it off first.

The axis motion is controlled by the X, Y and Z labeled + and – buttons shown above. Below those four buttons are selectors indicating the step distance from 0.02mm to 100mm. The selected axis will move the selected step distance with each mouse click. For this reason, please take special care when you've got 100mm set for the step distance. The Eris® is smart, but not THAT smart. It relies upon you to not put the poor thing in an unlikely position. :)
The “0.02” and “0.1” distance options can come in handy when you first start a print. If you notice that your first layer is either too high or too low, you can use one of these two distance presets to “bump” the Z axis higher or lower by a tiny amount.
The other highlighted items show the current locations of the three motion axes on the Eris®. The X and Y axes show as being in their “home” position, which is the center of the bed at 0,0. The Z axis describes the height of the hot end and it's at its home position of 170mm or so.
The last set of buttons control the extruder motor – they're marked E- and E+ and can be used to manually extrude filament. Note that they will only work if the hot end is up to operating temperature! The amount of filament extruded (or retracted) is set using the step selector below the control buttons for the extruder.

## 7 – MatterControl Basics: Loading & Printing an Object

We've previously worked with the small cube that MatterControl provided as an example. Now we're going to cover loading and slicing an object from start to finish.
For this section, I recommend you head over to http://www.repables.com and find something you'd like to print. I'm going to chose the SeeMeCNC “Blinky” logo token (http://www.repables.com/r/118/) (http://www.repables.com/r/151/) for my example print. You don't have to make the same choice, but pick something geometrically “simple” in order to make the learning process a bit easier.
Most (if not all) 3D printer slicing programs can read a file format called “STL”. (You can learn more about this file format, including its origins, here: http://en.wikipedia.org/wiki/STL_%28file_format%29) (http://en.wikipedia.org/wiki/STL_(file_format)) When you download a file from Repables or one of the other free, online object repositories, you'll often get the file as a zip file. One nice feature of MatterControl is the ability to select a zip file and MatterControl will transparently extract all the files it knows how to read and load them up into your print queue.
To load a file into MatterControl, make sure you're on the Queue page and click the Add button at the bottom right hand corner of the window.

Navigate to where you've stored the STL or ZIP file and open it using the Open File dialog that will appear.

I chose the Blinky Eyes token because it's got an odd little characteristic. The model was saved using centimeters as the unit of measure instead of millimeters. This results in a model that appears to be 10 times smaller than it really is!
This provides the opportunity to use MatterControl's model scaling feature. As you can see below, the loaded model is very, very, tiny!
Yep, that tiny little dot in the center of the build area is the model I just loaded. Fortunately, this is a really easy fix. Click on the Edit button that's located at the bottom of the model view pane.

That will activate the model editor so we can adjust the scale of the object.

The various edit tools are on the right edge of the model view pane. Click the Scale button and enter “10” in the Ratio field. Click the Apply Scale button to make the change.

Once the scale has been changed, your Blinky Eyes token should appear the same as the one shown below. Click the Save button at the lower right hand corner of the model pane to save your changes.

You can then click the Cancel button to exit the editor.

Tiny Blinky Eyes!

Save those changes!

Now that you've gotten the scaling adjusted, click on the Settings & Controls button so we can make sure you're using the right profile to print this object.
Click the Settings button and make sure that the Quality box is set to “Standard” and the Material box is set to the material preset you created earlier.

Before we start this print, let's take a second to examine a feature of MatterControl – the Layer View. If you've not sliced this object yet, you'll like see the text “Press 'generate' to view layers”. Go ahead and do that now.
When the slicing process finishes, you'll be

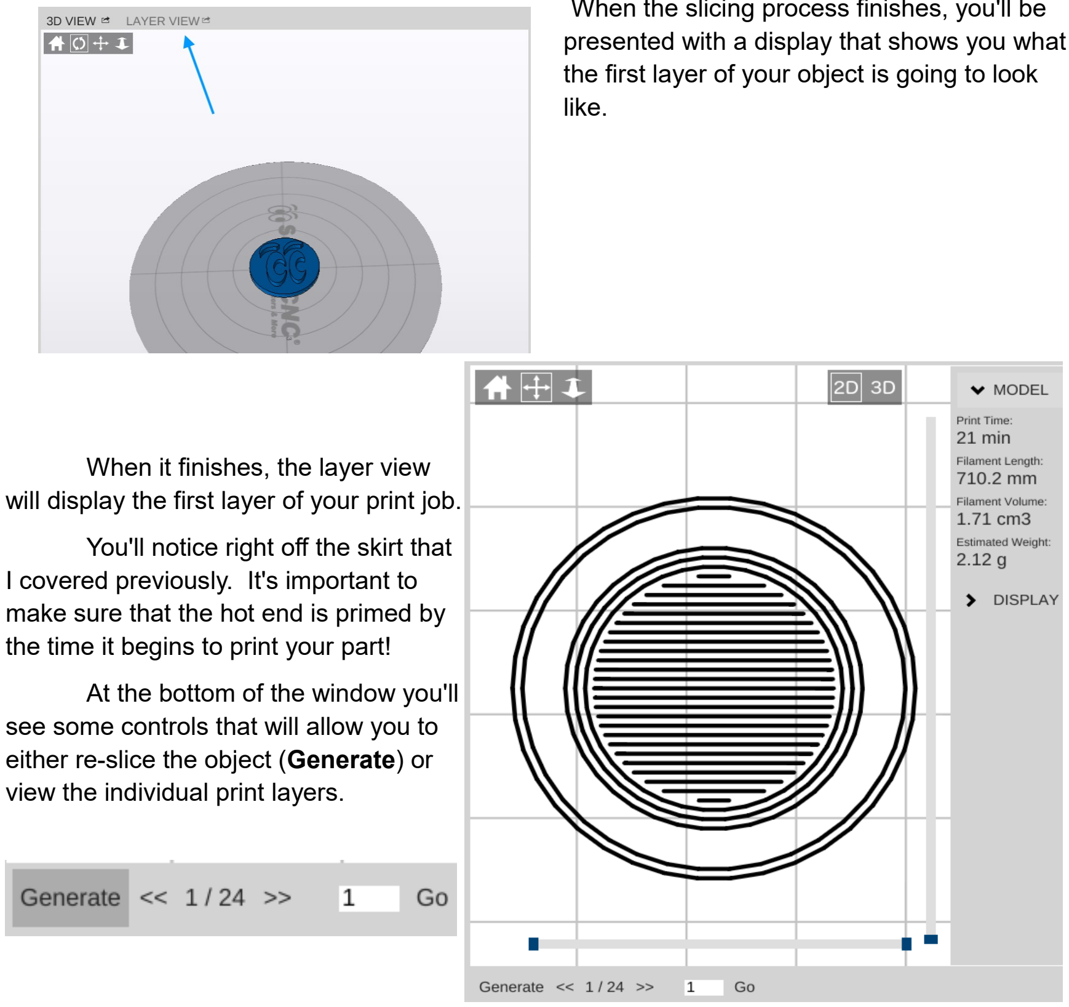
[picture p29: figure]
like.; When it finishes, the layer view; You'll notice right off the skirt that I covered previously. It's important to make sure that the hot end is primed by the time it begins to print your part!; At the bottom of the window you'll; view the individual print layers.

presented with a display that shows you what the first layer of your object is going to look

will display the first layer of your print job.

see some controls that will allow you to either re-slice the object (Generate) or

The controls will show you how many layers are on this object as well as what the layer number is that you're currently viewing. You can navigate forward and backward through the layers by using the >> and << buttons. If you want to jump to a specific layer, you can enter it in to the box and click Go.
After slicing the object, MatterControl will display a few

statistics about the current print in the Layer View window. This can
be handy information if you're selling your services and need to know how much a particular part is going to consume in both time and materials.
Go ahead and click the Print button and get your object printing!

Once the print job finishes, you should have a little Blinky Eyes token that looks like the photo below.

## 8 – Advanced MatterControl: Options

MatterControl includes a number of basic configuration options that you can use to set up things like your default slicing engine, change EEPROM settings, etc.
Let's go over each one as they appear on the MatterControl Options pane.

MatterControl includes a bed leveling feature that when properly configured, can assist with issues that can arise from an unlevel bed. I include this feature for completeness – since your Eris® has its own hardware calibration system, the one included in MatterControl is never used. In fact, unless you tell MatterControl that you don't have “hardware leveling”, you won't even see this option.

The EEPROM Settings configuration option will allow you to edit firmware parameters that are stored on the controller inside your Eris®. Please take special care when changing EEPROM values. An improperly set configuration parameter can cause your Eris® to misbehave. Sometimes rather dramatically. (One user reported something about his Eris® chasing the cat and yelling something about a “Smurf invasion”, but we haven't been able to corroborate that.)
Here's an example of the things you can change under the EEPROM Settings configuration:
Two fields you might be interested in are
“Filament printed” and “Printer active”. As you can
see from the display, the Eris® used here has printed 25.44 meters of filament for a total active time of 36,959 seconds (or roughly 10 and a half hours).

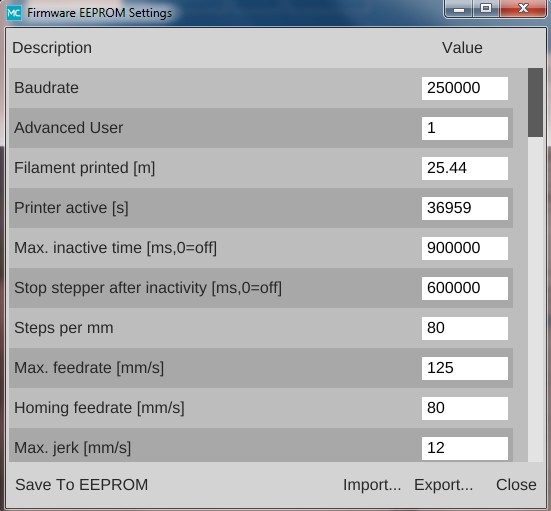
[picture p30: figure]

The Gcode Terminal is where you can directly interact with the firmware on your Eris® 3D printer.
When you first open the Gcode Terminal, you'll be presented with a window that looks similar to the one below:

You'll notice that the display will scroll as new information comes in from the Eris®. This is how MatterControl is able to continually update things like the temperature displays. In order to be able to use the terminal for basic tasks, you'll need to click on the Filter Output check box that's at the upper left corner of the window. This will filter out the telemetry information coming from the Eris®'s controller and allow you to directly interact with the printer without having the output interleaved with the periodic information that the Eris® transmits.

MatterControl provides the ability to remotely submit jobs or monitor your Eris® 3D printer from anywhere in the world. To learn more about the remote control feature, click on the “GO TO DASHBOARD” link and your browser will open up the MatterControl Cloud Sync website.
MatterControl also provides a few different settings that control how you can be notified when a print job finishes.
By default, MatterControl will play a bell sound when the current active print job completes. However, you can change this behavior via the Notification Settings configuration screen. You'll be able to configure MatterControl to send you an email or text message when your printer completes a job.

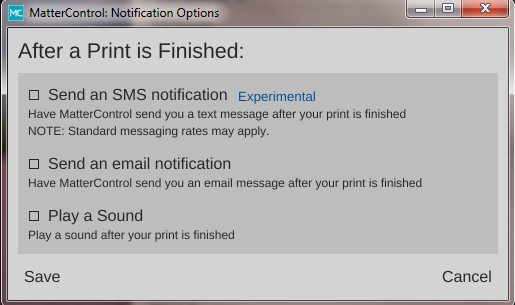
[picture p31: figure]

The Language setting allows you to change what language MatterControl uses when displaying the user interface.

The Slice Engine configuration will allow you to choose which slicer that you want to use in order to prepare your model for printing. By default, MatterControl uses the MatterSlice slicing engine that was developed by the MatterControl team. You also have the option of choosing Slic3r or CuraEngine to do your slicing. Selecting a different slicing engine will change the options available on the Settings pane, but shouldn't disturb those you've changed in the past. The MatterControl team has tried to keep common names across slicing engines, so the most noticeable change you'll see will be additional options supported by one slicer but not the others.

MatterControl offers two kinds of rendering for the thumbnail display that's in the upper left corner of the print window. See below for the two different options as they apply to the Blinky Eyes token you printed earlier:

MatterControl supports both the traditional mouse interface as well as a touchscreen interface. Display Mode dictates which of the two modes that MatterControl is operating in.

Clear Print History will remove all the items that are currently in your queue display.

Theme allows you to change the primary color that the user interface renders in. The top row of color selections provide the selected color against a light background. The second row of color selections provide the selected color against a dark background.

Rendered "flat" | Rendered "3D"

## 9 – Advanced MatterControl: Settings – Print

MatterControl offers three “classes” of settings that have a direct effect on how your printer works. General covers elements that relate to how the plastic is laid down. Filament covers parameters specific to the type of filament that you've chosen to print with. Printer handles those remaining parameters that describe the physical printer you're currently using to print with. This section will cover Print.
Let's start this overview on the main page of General, Layers/Surface.

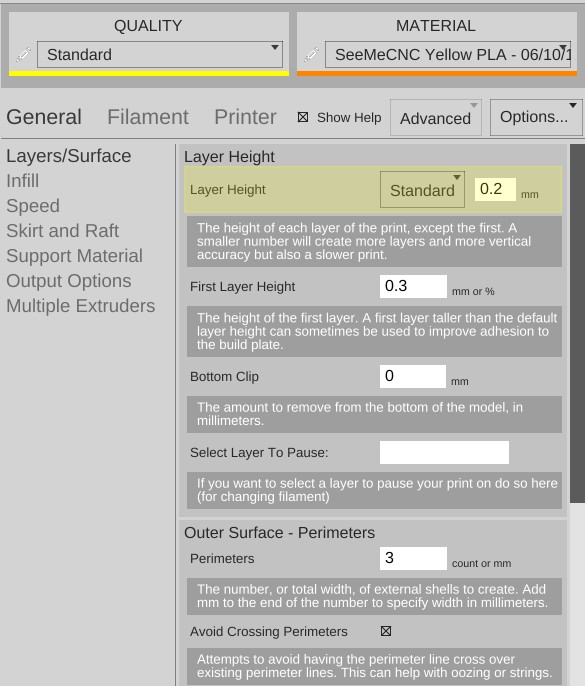
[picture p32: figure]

The first parameter is Layer Height. We've covered this one before, but I wanted to point out something that I didn't go into a lot of detail about earlier. You'll notice that the field has a yellowish highlight to it. That means that the value exists in the currently selected QUALITY profile. If you look carefully, you'll see that the highlight color matches the thin colored line under the QUALITY drop down. (This same effect holds true for MATERIAL profiles, but the color is orange.)
Any time you add a General parameter to a preset profile, it will be highlighted just as the Layer Height field is in the example. Note that you can use any of the General, Filament, or Printer configuration parameters within either of the QUALITY or MATERIAL profile editors.

The First Layer Height parameter allows you to set the thickness of your first layer. Having a thicker first layer will help provide a good base to build the rest of the part on as the thicker (and thus wider extrusion) will help improve the adhesion to the bed. If your first layer isn't any good, the part could eventually separate from the bed and ruin the print job.

Bottom Clip allows you to tell the slicing engine that you'd like to “clip off” a specific amount from the bottom of the model. For example, say you've got a 200mm tall model, but you only want to print the top 50mm or so. You can enter 150 into the Bottom Clip field and when the slicer generates the G-code for the print job, it will begin slicing 150mm up from the bottom of the model.

Select Layer To Pause gives you the option of telling MatterControl to pause the print at a specific layer. This is most often used when you want to change to a different color of filament for the current print job. When the print job pauses, MatterControl will lift the nozzle a few millimeters to give you room to purge the old color out of the nozzle when you change filament. You can use the Layer View in order more easily decide which layer you'd like to pause on.

Perimeters dictate how thick the “skin” of your model is. 2 or 3 perimeters are good for most parts, but if you want a really strong exterior wall, you can make the perimeter count as high as you feel you need it. To get an idea of how thick the skin will be, you multiply the perimeter count by the extrusion thickness (we'll get to that parameter in a bit). For example, if you have a 0.5mm nozzle, chances are your extrusion thickness will be set to 0.5. 2 perimeters will give you a skin thickness of 1mm. If you want a very specific skin thickness you can enter a value with “mm” as the suffix (ex. “1.2mm”).

When Avoid Crossing Perimeters is enabled, the nozzle path will not cross a part perimeter during travel moves. This will help reduce the opportunity for stringing or oozing since the nozzle tip is rarely over open air. For instance, if the tool path would normally cause the nozzle to travel from one side of the part to the other, it would cross at least two perimeters and may leave strings of material in its wake as it moves. If it is set to not cross perimeters, it will cause the nozzle to trace a perimeter back to the nearest point where it can begin printing again instead of jumping straight across to the new extrusion position.

Spiral Vase mode allows you to print things like vases or other open top, single-wall objects in one continuous layer. What happens is that instead of the slicer raising the nozzle up a full layer height for each new layer, it gradually increases the Z height as the print progresses. This results in a perfectly seamless object, which can be important for artistic prints such as vases. When you're printing a vase or similar object, you'll want to make sure that you set the top layer count to zero to prevent the vase getting a “lid” that you'll have to cut off.

By default, objects are printed from the inside features to the outside. If you want to reverse this process, enable External Perimeters First. This will cause the outside of the model to be printed before the interior features.

The Top and Bottom solid layer parameters dictate how thick the top and bottom surfaces of your object are when printed. These two parameters fulfill essentially the same function as the Perimeters parameter, but for the top and bottom of the part. You can calculate your top & bottom thickness by multiplying the solid layer count by the layer height. For example, 5 top layers will result in a final top thickness of 1mm if your layer height is 0.2mm. You also have the option of specifying an exact thickness in millimeters, using the same “mm” suffix used in the Perimeter field.

The next page in General is called Infill and covers how the interior of your part is filled. While I covered Fill Density and Infill Type earlier, the Advanced mode adds two new parameters.

The Starting Angle parameter allows you to control the orientation of the infill. For example, an infill type of GRID with a starting angle of zero degrees is going to look like this: Now if you change the starting angle to 45 degrees, you'll

end up with an infill pattern that looks like the example below.

Note that changing the starting angle
will also change the angle in which the top

and bottom layers are printed. You can see this in the image below – this shows the second layer as it would be printed.

Infill Overlap is used to adjust how well the infill pattern attaches to the inside perimeter of the part. A good infill will have a solid connection to the inside perimeter of your part, and the structural integrity of your part depends on this.

The Speed page covers parameters that control how fast various features of the object are printed. The speeds are listed in mm per second, or as a percentage of a related speed parameter.
The speed parameters are pretty
self-explanatory, especially if you've got
the Show Help check box set. However, there's a couple of points I'd like to cover about printing speed.
First of all, there is a relation between your print speed and the temperature you've set for the material you're printing with. The basic rule is, the faster you go, the hotter you print. This is because as the hot end extrudes plastic, it's constantly being cooled by the cold filament that's coming in.
Setting the extrusion temperature higher allows the hot end to melt the incoming plastic at a faster rate. This allows you to print more quickly. The relation between print speed and extrusion temperature is one of those
things you'll get a feel for as you gain
experience with your printer.

You'll quickly learn that the Eris® will “talk” to you if you're printing too rapidly for a given temperature. The extruder will begin to “skip” periodically (or frequently, depending on how fast you're going). A skipping extruder has a very distinct sound – it's kind of a light bump or knocking. If you watch the manual feed knob on the extruder, you'll notice that it will briefly rotate in the opposite direction at the same time you hear the skipping sound. The skip is caused by the hot end's inability to melt the material is rapidly as is required. The pressure builds up until the stepper motor can no longer generate the force required. At this point the tension in the filament is released like a spring and the filament pushes back with enough force to cause the stepper motor to skip steps, resulting in a short reverse rotation.
Secondly, there is also a direct relation between print speed and print quality. In the image above, you'll notice that the speeds for print moves vary a bit. This is because some features don't require a focus on surface quality.

Perimeters are a great example of this. You'll note that the inside perimeter speed is 40mm/sec, while the outside perimeter is 35mm/sec. The inside perimeter will never been seen after the print is finished so it can be printed at a higher rate. However, you want the visible surface of the print to be smoother and more consistent, so you print the outside perimeters a bit more slowly.
The last bit about speed settings I want to cover is the first layer speed. You'll see that it's really slow. The reason for this is that while hot plastic loves to stick to hot plastic, hot plastic doesn't like sticking to other things as much. By going slowly on the first layer, you're giving the material time to get a good grip on the surface of the bed. This is known as “part adhesion”. When a part comes unstuck from the bed during a print, it's ruined. This isn't so bad when you're five minutes into a print, but you'll be ready to flip a table when it happens 18 hours into a 19 hour print.
The Skirt and Raft page covers settings that control how the hot end is primed at the beginning of a print job as well as features that help the part stick to the bed.
The first section covers the Skirt
feature. A skirt in this context is basically a
series of single-layer loops printed around
the perimeter of the part. This acts as a method to “prime” the hot end with material

before the actual part begins to print. Loops
defines how many times you want to go
around the print. This is tied to the Minimum Extrusion Length parameter. If the number of loops you specify are not enough to meet that minimum length, additional loops will be added automatically.
The Distance from Object parameter dictates how far away the loop stands off from the part outline. If you set the distance to zero, the skirt will become a “brim”. It will result in the loops being printed connected to the first layer of your print. This can give small parts a first layer that has a larger surface area to improve part adhesion. Since the brim is only a single layer thick, it's usually pretty easy to remove after the print job has completed.

I mentioned earlier that hot plastic really loves
sticking to hot plastic, but not so much to other
things. If a brim isn't doing the job for you, you can
try a Raft.
When in Standard mode, the Raft setting was simply an on/off thing. In Advanced mode,
you've got a lot more control over how the raft is laid
down.
Expand Distance is the distance you'd like the raft to exceed the base area of the part you're printing. You may want to adjust this parameter if the part you're printing is larger than the bottom contact point on the bed. A larger raft will help to support the part more effectively.

Air Gap defines how much space you want between the top surface of the raft and the bottom surface of your part. This gap helps make it easier (or even possible!) to remove the raft from your part when it's finished. As mentioned in the help text, a good air gap is one half the diameter of the nozzle. For example, if your nozzle is 0.5mm, you'd want an air gap of 0.25mm. If you've added a second extruder to your Eris®, you can specify which one should be used for rafts by setting the Raft Extruder value to the index of the extruder you want to use. If you don't have multiple extruders, you can leave this set to zero.
The Support Material page provides

detailed settings on the use of support material if the
part you're printing requires it. While I covered the
basics of support earlier, I'm going to get a bit more
in-depth on it here.
Checking Generate Support Material will allow you to configure support for your part. Support is required when a part has an overhang or other angled feature that would result in little or no physical support to put a print layer on. The Support Type selection allows you to define the geometric pattern for the support structure. You have GRID and LINES. These patterns were covered earlier, so I won't cover them again here.

Pattern Spacing controls the distance between each “track” of support that is laid down to support your part. The wider the spacing, the less support that is printed.

Support Percent tells the slicing engine that it should generate support for layers that have an overlap of less than the specified percentage. In the setting shown above, the slicing engine will generate support at points where the model layers overlap 50% or less.
When you've got a part feature that's only 20 degrees or

so, each layer can easily be supported by the layer underneath. This is because as the part height increases, the horizontal dimension increase is less than the extrusion width. This means that each new layer has a solid foundation to adhere to as it's being applied. At 20 degrees, you can see the layer overlap is right around 80%.

As you can see when your angle increases to 45 degrees, each layer has much less surface area to adhere to as you print. This is where support comes in handy. It provides that underlying structure for those layers to build upon.
As the angle increases, the underlying surface area for each layer becomes smaller and smaller until there's simply not enough surface for the next layer to adhere to. In these

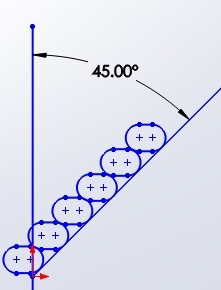
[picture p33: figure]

instances, support material is practically a requirement if you want your part to print at all.

Infill Angle adjusts the angle at which the support structure is built.

Interface Layers allows you to specify solid layers interspersed with the support material. This comes in handy when using multiple extruders. For example, if you're printing a part in PLA with lots of support, you can generate all the support with PLA, and then have 5 or 6 interface layers of PVA (a water soluble filament). The print would then only be in contact with the PVA interface layers and it would be a flat layer to print on. When finished you can dissolve away the interface layers and the rest of the support falls off the part cleanly.

45 Deg. Infill

X and Y Distance dictates how far away the support structure will be from the part you're printing. You want it as close as you can get it without it actually touching the surface of the part. The default of 1mm seems to work out pretty well.

Air Gap specifies how many layers should separate the support material from the part. This parameter contributes to how easy or difficult it is to remove support material from the part once the print is finished. If you have too little gap, the support material will have more of a grip on the part surface making it difficult to remove. If the gap is too large, the support material won't be able to do its job very effectively.

If Support Everywhere is checked, you're probably going to get more support material than you bargained for. If you have an internal feature of a part, this may be required in order to support it, but keep in mind that it will also add support to features like horizontally oriented holes, which don't normally need support to print properly.

Create Perimeter will generate an outline around the support material in order to improve its strength and hold up interface layers.

If you've got multiple extruders on your Eris®,
these parameters allow you to specify which extruder is used for generating support structure.

On the Output Options page is a single parameter, Center On Bed. This will automatically center the model on the print bed when you load it. If you don't want that to happen, just uncheck the box.

The Multiple Extruders page has two settings that control how ooze & filament wipes are handled.

The Wipe Shield Distance specifies how far away from the part you want what is commonly known as an “ooze shield” to be placed around the part. In a two extruder system, the unselected hot end will create this “shield” in order to avoid dripping or oozing plastic on other parts of the model.

Wipe Tower is used when changing extruders. The active nozzle creates a tower of the specified size and will use it to wipe the nozzle in order to reduce the possibility of oozing or dripping material on the model while the other extruder is active.

## 10 – Advanced MatterControl: Settings – Filament

The Filament tab allows you to change parameters that deal with the current filament you're printing with. The Filament page is divided into three categories; Filament, Temperature, and Retraction.
The filament Diameter parameter tells the
slicing engine the size of the material you're
printing with. When starting a new roll of material,
you should pull off about 2 meters of material and
check it in 10 spots along the length using a digital

caliper. Average those samples and plug the result into the Diameter field. This is a good way of getting a good estimate of the material you're actually using. This allows the slicing engine to deliver more consistent results instead of depending on the generic size of the material.
You'll notice that the Diameter field is highlighted in orange. This means that the parameter is part of a predefined material configuration. When using a new spool of material for the first time, it's a good idea to create a new profile for it when you're taking the sample measurements of the diameter. A good rule of thumb is to include the date you started using the filament as part of the material profile name. Note the date on the spool label if it has one and add one if it doesn't. This will help you track individual spools of the same color and manufacturer.
The Extrusion Multiplier parameter allows you to tweak the flow rate of the material coming out of the hot end. A basic rule of thumb on this is to restrict the max value to 1.1 and the minimum value to 0.9. Note that these aren't hard limits but are simply a guideline to utilize until you're familiar with the effects this parameter has on print jobs.
The Extruder Temperature is the
temperature for the hot end. Each material
class has a general temperature range for
the hot end. For example, ABS extrusion
temperatures can range from 195 to 240C.

PLA likes anywhere from 180 to 215. The specific temperature that your material works best at varies by manufacturer and chemical blend. It's not unusual to see different “sweet spot” temperatures among identical colors of material, even with the same manufacturer.
Extruder Wipe Temperature is only used on those printers that have a special hot end “wipe” feature that can be used to clean the nozzle before a print begins.

Retraction covers how the slicer “retracts” the filament during travel operations where it's not actually laying down plastic. Good retraction settings help keep your part free of little strings and blobs during printing. Length on Move specifies how much filament will be backed out of the hot end during a non-printing move.
Length on Tool Change is specific to multi-extruder systems. If the slicer is changing to a new extruder, it will retract the material out of the current hot end by this much. This works in conjunction with wipe towers and wipe shields.
Speed dictates how fast the extruder drive will pull the filament out of the hot end.
Higher speeds can assist in preventing
already-melted plastic from oozing or leaving

strings on the part being printed. It also controls how fast the filament will be returned to the hot end when the non-printing move has completed.
Z-Lift is used to lift the nozzle off of the part as each retract finishes. This can help prevent blobbing.
Minimum Travel Requiring Retraction is used to prevent retractions during very short moves when retraction isn't really necessary. When executing a non-printing move, the nozzle will have to travel at least this distance in order to trigger a retraction action.
Minimum Extrusion Requiring Retraction specifies how much filament must be extruded before a retraction operation is permitted. This helps prevent instances where a retraction operation would occur before the hot end had the opportunity to actually extrude material.
Retract When Changing Islands if checked, will trigger a retraction when the nozzle is traveling to a different “island” on the current layer. (An “island” is any place on the current layer that has an air gap between it and another “island”.)
Wipe After Retract is used to “wipe off” the nozzle by retracing up to 10mm worth of travel before continuing on. This can help with stringing issues.

The next page is called
Extrusion and contains a set of parameters for dealing with the width of the material as it's extruded.
The First Layer parameter
allows you to specify the extrusion
width of the first layer. A first layer
width that's larger can help with how

the material adheres to the bed. You can specify it as either an actual width, or as a percentage of the normal extrusion with (typically the same as the nozzle diameter).
Outside Perimeters will allow you modify the width of the extrusion when you're printing the outside perimeter of the model. This can come in handy if you need to fine tune the exterior dimensions if they don't exactly match the model.
Support Material allows you to specify how wide you want the extrusion to be for the support structure if you're using it.

The Cooling page covers parameters relating to layer cooling.

Cooling Thresholds allow you to slow
the print speed down during a print if needed.
If the current layer will require more than the specified time to print, the slicing engine will
automatically slow the print speed down to

meet this goal. This can be important because
if you don't use a fan, a layer will need time to radiate its excess heat before the next layer is applied. If the material isn't cooled, or given time to cool via radiation, heat can build up in the underlying layers and cause curling and other undesirable effects.
Minimum Print Speed can be used to ensure that the printer doesn't slow down TOO much, which can cause it's own heating problems. For example, if you're printing too slowly, the presence of the nozzle moving over the surface can cause heating to areas adjacent to the nozzle tip which can cause blobbing or layer deformation.
Note that there are fan options that be present if you've enabled the operation of the fan. Because the Eris® has a combination cooling solution that covers both the cold section of the hot end and the layer cooling feature, the individual fan options are disabled by configuration option.

## 11 – Advanced MatterControl: Settings – Printer

The Printer section covers items that are specific to the printer being used for the current print job.
The Print Area page covers
parameters that describe the
mechanical features of the printer. The Bed Size fields cover
the width and length of the bed. Since the Eris® has a round bed, you'll see that both figures are the same, the Print Center has been set to 0,0 (the center of the circle)
and the Bed Shape has been set to
circular.

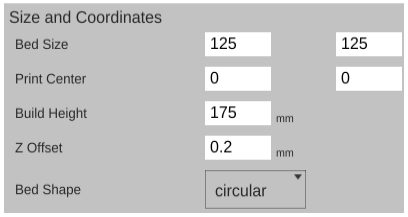
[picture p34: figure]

The Build Height parameter should be set to the highest practical build height. In the case of the Eris®, this is set to 175mm. (The actual maximum Z height recorded in the
EEPROM may differ due to being updated by the auto-calibration routine.)
Z Offset can be used if you want to set a specific adjustment to the z-zero position of the G-code when it's created by the slicing engine.
The Bed Shape parameter dictates what bed type is shown in the 3D viewer.
The Hardware section allows you to specify what features are installed on your Eris®. Has Fan, when checked will allow
the slicing engine to control the layer
cooling fan.
Has Hardware Leveling should be set for the Eris®.
Has Heated Bed should be
unchecked for the Eris®. This allows the slicing engine to control the heat of the bed when one is installed..
Has SD Card Reader should be unchecked for the Eris®. This allows MatterControl to save STL and G-code

directly to the SD card if there's one present
on the currently connected printer.
Has Power Control should be
unchecked on the Eris® as it does not support that feature.

Show Reset Connection should be checked on the Eris®. It will present a “Reset Connection” button in the printer connection bar that can be used as an emergency stop.
Show Firmware Updater should be set to “Simple Arduino” for the Eris®. This controls a feature that allows MatterControl to send firmware updates directly to the printer.
For a stock Eris®, Extruder Count should be set to 1. If you add an additional extruder in the future, you can tell the slicing engine about it here.
Heat Before Homing will force the nozzle to heat up to operating temperature before homing.
Share Temperature is used when utilizing multiple extruders that share the same heat source.

The Firmware section allows you to tell the slicing engine about the firmware you're using with your Eris®.
G-code Output specifies what

“flavor” of G-code should be created by the
slicing engine. For the Eris®, this should be set to REPRAP.

The next page is called Custom G-code and allows you to customize the code sent for five different print events. Unless you're familiar with what the listed G and M codes do, please don't modify the defaults shown.
Start G-code is inserted into the
G-code output right after the temperature
setting. If you have the commands to set the temperatures in this section, they

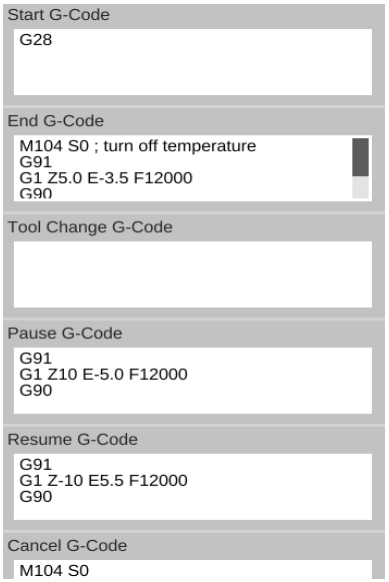
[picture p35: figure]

won't be generated outside of this section. You can also include values from other sections such as “first_layer_temperature” End G-code is inserted into the output at the very end, after all print operations have been completed.
Pause G-code is sent when the Eris® is paused during a print.
Resume G-code is sent when the Eris® is resumed.
Cancel G-code is sent when you cancel a print job from MatterControl

The last page for the Printer tab is called Extruder. This page allows you to configure each extruder you have installed in your Eris®.
Nozzle Diameter specifies
the diameter of the currently
installed nozzle in the hot end.

Extruder Offset allows you to specify the offset from the center of the effector platform in the Eris®. This parameter is only used in multi-extruder configurations.

The last feature I'd like to cover can be found here:

The Options control allows you to import and export configurations. This can be handy when you want to share your slicing engine settings with others, or import settings from other sources.

## 12 – Using the 3D View and Layer View

The 3D View will show you the part that will be printed when you hit the Print button. The Layer View is used to inspect how your part will be printed, one layer at a time.

The 3D View will allow you to view your model in pretty much any orientation you'd like. The view orientation is controlled one of two ways. You can select one of the movement icons in conjunction with the left mouse button. The first icon will reset the view. The second icon will allow you to “free rotate” the model and build platform. The
third icon will allow you to move the part and build platform left
and right, as well as up and down. The fourth icon will allow
you to zoom in and out.
You can use the mouse alone as well. Holding down the left mouse button will allow you to “free rotate” the model and bed. Holding down the mouse wheel will allow you to move left and right as well as up and down. Spinning the mouse wheel will zoom in and out.

The 3D View will also allow you to directly manipulate the part or parts currently being displayed on the virtual print bed. The first control, Insert is
used to add one or more components to the virtual print
bed. To give you an idea of how this works in practice, head
over to Repables and grab the “Ignite Michiana” object – http://repables.com/r/146/. MatterControl is pretty smart – you don't have to extract the STL file from the ZIP file. Click on Insert and navigate to where you saved the downloaded zip file and select it. When the file is loaded, your screen should look something like this:

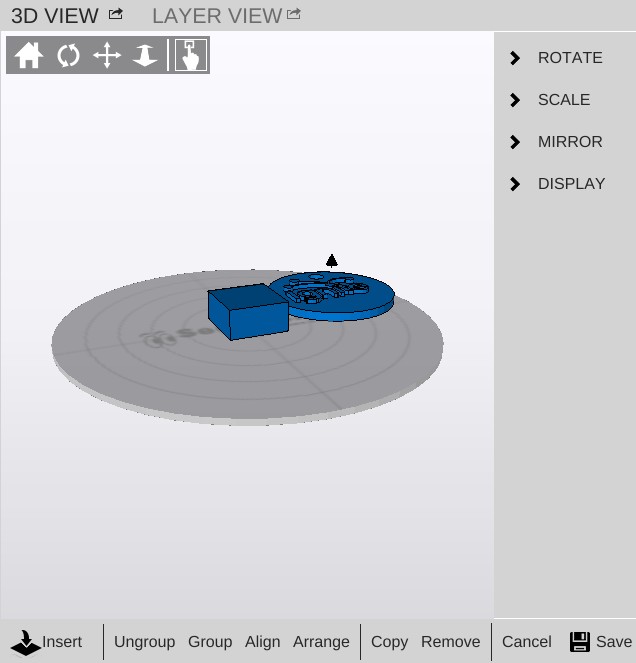
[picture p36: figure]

If you didn't already have the example cube loaded, you may only see one object in the center of the bed. If this is the case, go ahead and load another Ignite object.
Click Save to “commit” the newly inserted model to the build plate.

You'll end up with something similar to the figure below after clicking on Auto-Arrange. The blue arrow points to a tiny icon that indicates which is the currently selected object. In order to move an object around manually, you'll need to make sure that the “picker” icon
has been | selected.

Once you've clicked on that icon, you'll be able to move the parts any where you like. However, be aware that the software will allow you to move the objects outside the confines of the virtual bed and they will not be printable outside of those limits.
You'll notice that you've got some new

controls along the bottom of the 3D View window – Ungroup, Group, Align, Copy, Remove, Cancel, and Save.
The Ungroup button will undo the “grouping” done by the Group and Align buttons. Clicking Group will virtually connect all the objects on the print bed so they can be moved all at the same time.
The Align button has the same effect as the Auto-Arrange button, but the resulting group of objects are not centered on the virtual print bed.
Copy allows you to create duplicates of objects that are on the print bed as shown below. Make sure that you've got the object you want to copy selected before you click the Copy button.
Be aware that if you've got
your objects grouped, clicking on
Copy will result in the entire group being copied.

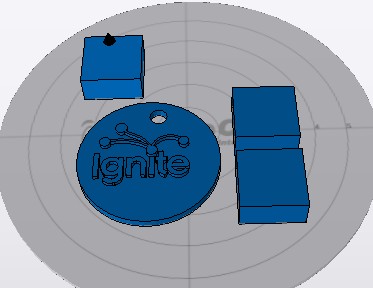
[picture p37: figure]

The Remove button works as you'd expect. Select an object and click Remove to remove it from the virtual build surface.

Cancel will discard any changes you've made so far and Save will allow you to save the state of the virtual print surface. Saving your work saves it to the print queue. Note that if you've clicked on Save, the Cancel button will retain your changes and just exit the edit mode. While you're in edit mode, there's a series of commands that
become available along the right edge of the 3D View pane.
Unlike normal manual positioning, the
Rotate function allows you to specify the exact
rotation of the object along its X, Y, and Z axes.
In order to change the orientation of the object, simply enter the value you want in the

Degrees field and then click the axis you want to apply that value to. Below is an example of what the example cube looks like after rotating it 45 degrees along its X axis.

Being able to re-orient the part on the build surface can be handy to have, especially if you're dealing with a part that was saved in a position that didn't lend itself to easy 3D printing.
Clicking Align to Bed will automatically orient the nearest flat surface to the virtual build platform. You can see in the example below what happens when you click Align to Bed on a rotated part.

The Scale function will allow you to change the width, height and length of the part or parts currently on the virtual build platform.
The Ratio field allows you to shrink or grow an entire model by a specific percentage. For example, if you were to change the Ratio from 1 to 1.5, you'd see this:
Become this:

The scaling operation made the cube 150% larger than the original. The X, Y, and Z fields allow you to specify exact dimensions. However, as long as the Lock Ratio field is checked, any change made to those fields will adjust the others to maintain the same ratio. The Mirror function will simply allow you to “mirror” the object along any of the three axes. Note that mirroring the Z axis will flip the part upside down, so be careful.

The Display function allows you to modify how the 3D View pane operates. Show Print Bed is pretty obvious. Uncheck it and see what happens! Shop Print Area is handy when you want to see exactly how much space your parts are going to take up. When selected, it will display a shadowed cylinder that encapsulates the maximum bed diameter and print height, as show below.

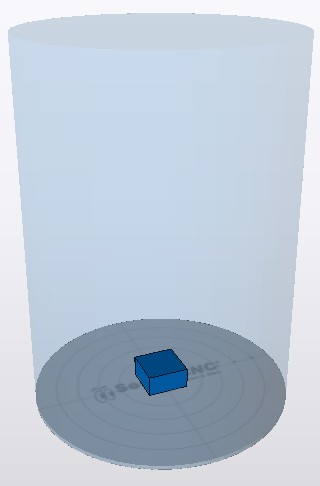
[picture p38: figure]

The Shaded, Outlines, and Polygons options allow you to change how your objects are drawn. By default the Shaded option is checked. For most parts this is fine, but if you'd like to see detail that the solid shading can hide, click Outlines. Models used for 3D printing are built out of a few up to many thousands of polygons. If you'd like to see what the polygons look like that make up your model, click the Polygons option.
I find that the Outlines display option is the most useful as it makes part detail much more easy to see.
Shaded | Outlines | Polygons

The Layer View is where you can see exactly what the Eris® is going to do while printing your part. When you first select it, it may show “Press 'generate' to view layers”. Click the Generate button in the lower left corner of the Layer View display. This will hand over the parts to the slicing engine and will create the G-code required to print your parts.

In the image above, you can see that the parts have been sliced and layer #1 is being displayed. Along the right side of the display, you'll see a printing time estimate as well as an estimate of how much filament will be required to print the two parts shown.

There are two “scroll” bars shown in the Layer View. The bar along the bottom will show progress of the current layer, while the vertical bar will show layers. Using the << and >> buttons along the bottom, you can step through the layers one at a time, or jump to a specific layer and click on the Go button.

The Layer View will also allow you to see the layers in 3D. Just click the 3D icon at the upper right corner of the display window to see your layers in 3D! The display can be moved around in the same manner as that shown for the 3D View.

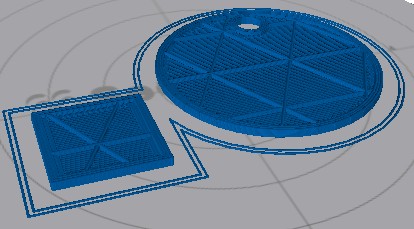
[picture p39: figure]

The Layer View will also display other information about the printing process, such as non-printing movement, retractions, etc.

7 Layers in.

9 Layers in, 3D view.

Click on the Display button to the right of the display to open up those display options. Print Bed hides or displays the virtual print surface.
Moves will show you the path the print head takes when it's not
printing, as shown by the light green lines in the image below.

Retractions show the points in the print where the extruder is going to retract filament from the hot end. This is done either during a non-printing move, or when changing extruders. The red and blue points in the image to the
right show where the retractions are happening.
Red shows the retract operation while the
blue color shows the resume/extrude.

Speeds will color the layers based on how fast the layer is printed.

The Extrusion option will thicken the lines
used to draw the layers in order to give a more accurate visual representation of what the actual print layer will look like when printed.
Finally, Sync to Print will allow you to follow the print process using the Layer View. As the Eris® prints your part, you'll see a real-time reflection of those moves. It's a pretty nice feature.

## 13 – A Strategy for Successful (and Great!) Prints

Michael Hackney is one our forum moderators over at the SeeMeCNC forum and he's been gracious enough to allow me to publish his wonderful guide for getting the most out of your SeeMeCNC 3D printer. You can find his original thread here: http://forum.seemecnc.com/viewtopic.php?f=36&t=7361
Some of the links below reference part files that are stored on the forum itself. You may need to create a forum account to reach them. I highly recommend doing this whether or not you need the files. The SeeMeCNC is an excellent resource with a vibrant, helpful and very newbie-friendly community.
I've watched folks struggle to achieve the results they want/expect here for several years – heck, I was one of us. Like all new endeavors, there IS a learning curve with 3D printing. This is still the pioneering era for desktop printing and we are very fortunate to have such a great community here as well as other resources on the web. But the challenge with all the information out there is finding it when YOU need it and deciphering the many different opinions and practices - some of which are good and some of which are, well, let's just say "poppycock". There are many different means to the same end but I assert that those who figured something workable (AND reproducible) out most likely took a disciplined approach to reach their goals rather than the shotgun approach of trying one thing after another. So, I thought it would be helpful to describe a method that you can use to 1) develop a reproducible approach to successfully printing the things you want and 2) improving the quality of your prints to meet your (realistic) expectations. I'll likely do this as a series of posts starting with this one. Don't hesitate to join in or ask questions. After some time, I'll consolidate the posts into a single source (maybe a pin here) that will make it easy to find.
On board? Let's go!
#1 Get Experience.

Start with the printer. This is more difficult than it seems because without experience, it is hard to know if you have a mechanical or electrical issue, slicing issue or if something else is going on. So, to that end, keep things simple until you have some experience. By "simple" I mean, don't print the Eiffel Tower model to start, print a simple, reproducible and small item many, Many, MANY times until you nail it. For me, I used the calibration cube. In retrospect, I should have picked something much simpler (see strategy #2).
#2 Start Simple.

We have a tendency to want to jump ahead to more complicated prints, faster printing, bigger prints, etc. There are many aspects to successful 3D printing, everything from the printer (which in itself has a mechanical system, electronics system, hot end, extruder, heated bed, firmware), to the slicer (and all of the parameters available to control the slicing), to the filament itself, to the actual item being printed. With so many variables (100s, maybe 1000s of them) it is really important to pin down as many of them as you can.

One very easy place to do this is with the model itself. Develop your experience printing the same model over and over until you nail it. Even with a simple model, you can (and should) approach printing it with a methodical approach from the ground up. That's the next strategy. #3 Practice in Measures.
I play guitar and was basically self taught. When I found new music to learn, I did what many untrained folks do and practiced the part over and over again from beginning to end. If I made a mistake, I started over. Then, I took lessons from a trained musician. My very first lesson was worth every penny! My instructor watched me learn a piece and then said "Practice in Measures". What he meant by this was to learn the first measure (music is divided into small blocks of notes called measures which are small and relatively simple). Practice it until it is perfect. Then, practice the second measure until it's perfect. Next, combine the first and second measures until that is perfect. Continue in this way until you've learned all the measures and combinations of them. In complex pieces, there will be a few measures or sequences of measures where you need to put in a lot more practice.

The advantage of this approach, my instructor said, is that you are not wasting lots of time playing measures you already know. The practice of playing from the start until you reach a difficult spot and make a mistake is that you play, say, 30 seconds (or more) of music you already know to hit a 1 second spot you need to practice. So in a 30 minute practice session you are really only practicing what you need to practice for 1 minute! This completely changed my approach to practicing everything from guitar to 3D printing to machining to learning CAD, to ...

How does this apply to 3D printing? Easily, start with a simple object to print and practice nailing the first layer. Once you have that nailed, print the rest of the object. Once you have the entire object printed successfully, change slicing parameters and start over (nail the first
layer, ...). Practice in measures.

I can't say enough about getting that first layer right, the subject of the next strategy. #4 Nail the First Layer.
I don't believe folks spend enough time learning to print a perfect first layer reliably. If there are defects in the first layer, they will invariably come back later to bite you - the part separating form the build plate or a defect in the part. Trying to print a good (or great) first layer is probably one of the most frustrating experiences for most, it is also the most critical. Here's where strategy #3 comes to play, don't continue a print on an inferior first layer! Abort the print and start that first layer again and again until you nail it. Why waste time on a part that will most likely fail or not be useful? Each time you print a first layer, measure it! If you tell your slicer to print a 0.20mm first layer, then it should be pretty darn close to 0.20mm. If it isn't, you've identified a variable that you can easily fix and nail down (Z height). 0.20mm is not a lot and unless you have highly calibrated eyes, you can't tell the difference between 0.20 and 0.15mm, but your printer sure can. At 0.15mm the first layer is going to squish onto the print surface.

It may even seem like you are getting a great first layer and great sticking (which you are) but later, you'll discover the part is nearly impossible to remove or your extruder will start making that all too familiar TICK, TICK, TICK sound from missing steps. A perfect first layer will go down smooth and consistently time after time.

TIP: polish the tip of your nozzle! Charred filament and scratches on the very tip of the nozzle are dragged over the layers as it moves around. Best case these leave a visible mark on the print, worse case they rip the first (or higher) layer off the build plate.
#5 Slow Down.

Back to my guitar lesson example... The other thing my instructor taught me in that first lesson was to practice slowly (using a metronome) until I nailed the measure(s) at a slow tempo. Then, gradually and consistently, increase the speed. The same applies to 3D printing, print slowly at first. This gives you time to observe what's going on (strategy #6) and just simplifies everything. I like to start new folks at 20 to 25mm/s print speeds. What's the hurry? If you print 10 aborted prints at 50mm/s what have you gained (or lost)? Printing slow helps all parts of the printer, from the mechanics to the extruder to the plastic filament coming out the nozzle, stay in balance or equilibrium. Fast movements can highlight mechanical issues, extrusion issues, etc. But when you are first starting out, you don't know how to identify and isolate these issues. In fact, even with all of my experience, if something starts to go wrong, I slow down. That removes a lot of variables and gives me a chance to see what's happening. I've identified everything from loose pulleys to a worn joint on a delta arm to separating arms on magnetic ball joints! And, I've helped a lot of folks identify other issues simply by slowing down.

#6 Watch What's Happening.

Especially in the early stages of learning, watch all aspects of the printer. Combined with strategy #5 you'll start to develop an appreciation for how the slicer does its magic, how the printer does its magic, and it is just simply fun to watch (especially a delta printer)! I highly recommend putting a flag of some type on your extruder so you can actually watch retracts and advances and watch the steady push of the filament. A piece of masking tape stuck to the shaft is fine or print one of the pointer models. Watch that first layer print, that's how you'll see if there is a problem and maybe even figure out why. For example, I noticed that the first layer wasn't sticking in the same spot on my build plate. Turns out that I had some potato chip grease there (don't ask)! A little wipe with isopropyl alcohol and I was back in business. Watch what happens when the layer fan comes on. Is it coming on too early and causing the part to peal from the print surface? Pay attention to the details of what's going on and then...

#7 Keep Notes.

I can't stress how important it is to keep notes. I have a word processor file I add notes to as I go. In particular, I keep a section on the filaments I use and the detailed printing parameters for them (strategy #9). Perhaps I'm becoming forgetful in my advanced age but I don't like solving the same problem over and over again. If I keep a note about a problem and my solution, I can usually find it again pretty quickly. Once comment on notes, don't be afraid to purge! After a few years of doing this, my file got quite big.

Recently I archived all of my H1 and H1-1 notes. I don't refer to them any longer so why keep them in my working notes?

#8 Be Consistent.

A CEO friend I worked with many years ago was fond of saying "Consistency is the hobgoblin of small minds!". I understood what he was trying to say but it has to be taken into context. When you are first learning any new activity, it is critical to be consistent. If too many things are changing at once, you have no idea what contributed to a good or bad result. Don't change too many things at once. In fact, if you can isolate and change just ONE thing, you will have a much better chance of success and understanding. This isn't always possible so lock down as many things as you can. If after a run of successful printing you run into a problem, go back to a known good state (see #7 - you did keep notes on what this state was didn't you?) and start there. Many times we try to change too many things in our frustration and that almost always makes things worse. Step back and think about how to isolate the problem areas with as few changes as possible.
#9 Know Your Filament.

This strategy is a bit lower level than the previous eight but important and often overlooked. I see a lot of folks just assume that they should print filament X at temperature Z -for instance, print PLA at 200°C. This might get you in the ball park but if you really want to get to consistent and GREAT results, profile your filament. It's easy and if you write it down (see #7) you'll never second guess how best to print that filament again. It's important to realize that higher temperatures are not always better, they can actually lead to issues - parts that are just a little too large, parts that stick to the bed too well and can't be removed, blobs on the print, stringing, and a host of other problems. In general, I like to print at the lowest temperature possible for PLA and ABS. Then, as I ramp up print speed, I also need to ramp up the hot end temp a little since the filament is not resident in the hot zone for as much time. I suspect little details like this cause people more problems than they might anticipate.

Here's how I profile a new filament:
- Start with a reasonable target temperature - 200°C for PLA and 225°C for ABS (one quick note, it is ideal to have a calibrated hot end, so when I say 200°C I mean 200°C. One easy way to do this is to make a little table with the hot end set temperature (what you see on the temp display) and the measured temperature (with a thermocouple). Do this in 5°C increments from 160° to 240° C (or so). Keep this chart in your notes (#7) and you will always know what the actual temperature is.)
- Now, use the manual controls of your host to extrude 50mm at 50mm/s and watch and listen.
- If the filament extrudes nicely, reduce the temperature by 5°C and wait for the temperature to stabilize.
- Test again by extruding 50mm at 50mm/s
- Repeat until you reach a temperature where the filament does not extrude well. At 5°C to that temperature and note this as the "low extrusion temperature" for that filament. Use this low temperature whenever you are printing slowly (20-30mm/s). You might find some filament need to be bumped up a bit more than 5° so don't hesitate to experiment and find that lowest reliable extrusion temperature.

If you want to get really serious about profiling your filaments, do the melt-flow test at higher extrusion rates - 60 mm/s, then 70mm/s, etc.

Don't forget to measure the diameter of your filament too! Not all filaments are created equally. Measure in several locations to get a sense of variability. Most of the slicers let you enter filament diameter and they will calculate a reasonable flow for you.
TIP: When you are starting a new print session, give the printer a little warm up exercise! Much like an athlete warms up before a game, don't just turn the printer on and attempt to print. Turn it on and let the hot end get up top equilibrium, let the heated bed get up top temperature. I even like to print a quick part (a 20mm diameter cylinder 5 mm tall) to make sure everything is up to temp, in equilibrium and working properly. It's quick and easy to do and can help eliminate a lot of problems.
#10 Know Your Bedfellows.

Probably one of the greatest mysteries in 3D printing is "the bed". Metaphorically, this is where the rubber (filament) meets the road (bed) and getting "it" right is absolutely critical to successful fused filament 3D printing. All sorts of folklore on bed materials, coatings, coverings, concoctions, and juju exists here and elsewhere on the internet. It is also one of the areas that there is no one right way to do it. If you have discovered a special incantation and bed preparation that works, by all means stick with it! But, for those of you struggling, here are some strategies you can use to make improvements. One comment before I begin...

I am VERY persnickety about the aesthetics of my 3D prints. My 3D printed fly fishing reel is seen from all sides and so it is important that the first layer is flawless and visually appealing. A perfect first layer finish is not required for all objects - consider the base of a Yoda or vase - but if you practice getting a great first layer on these non-critical pieces you'll be prepared when you need a visually perfect first layer on another project.

A number of factors affect adherence of the first printed layer to the bed. These include:
- surface material
- surface texture
- surface treatment/coating
- bed temperature and uniformity of temperature
- air temperature
- chemical bonding or cohesion
- print speed (see #5)
- filament temperature (see #9)
- first layer height (see #4)
- cleanliness (of bed and filament)

This isn't an exhaustive list but it does include the big hitters and, as you can see, there are a few of them so it is very important to take a methodical (#2 and #8) and documented (#7) approach when solving bed-related problems. This is also a place where careful observation (#6) can play an important part.

I'm not going to go through all of these in detail now but did want to comment about the last one - cleanliness. Whatever you do, make sure everything near and on your printer is clean and grease free. Silicone greases and lubricants are especially problematic since they are invisible and very difficult to remove. Keep them away from your machine.

Your fingers are a prime source of contaminants. Every time you touch the filament or bed, you risk leaving a greasy print (see my observation in #6) and these can (and will) cause issues. I try not to handle filament with my bare fingers, I use cotton gloves. If you use a plastic or rubber glove, make sure it isn't coated or powdered - we're trying to eliminate sources of contamination, not introduce them. On the occasions that I do handle filament with my bare hands I wash and dry them thoroughly first. This is one area that I think affects a lot of user's and is completely overlooked. How many times have you loaded filament right after eating chips? It introduces a big variable that can be difficult to track down, so develop good habits and eliminate contamination as a variable.

Your fingers can also leave contaminants on the bed when you remove a part or brush off stray filament strands. Don't touch the bed surface if at all possible. If you do, clean/degrease it with an appropriate cleaner. For uncoated surfaces like borosilicate glass, PEI, the various 3d party surfaces (PrintInZ and BuildTak), and films (window tint, Kapton) you can use isopropyl alcohol. I like to use the little packages of wipes as they are convenient and safe. You can also do a quick wipe of your fingers before tossing it in the trash. It is more difficult to deal with coatings like PVA glue, glue stick, and hairspray since these can't be cleaned. If you suspect a contaminated coating, your only recourse is to remove and reapply it.

Finally, don't overlook filament storage, keep it clean too. I store mine in large zip lock bags to keep off dust. You can put packets of desiccant to help remove moisture in the bag too.
#11 Learn to Diagnose.

Patient: "Dr. it hurts when I move my arm like this."
Dr.: "Then don't move your arm like that!"

The first point of this joke is, many people do the same thing over and over again without making any changes or stopping to think about what to change (see #8: remember, change one thing at a time) - as if just repeating the same print with the same parameters will magically solve the problem. It won't (see my footnote below).

The second point of the joke is that the Dr. didn't attempt to actually determine why the patient's arm hurt, he just had him avoid the problem. I see that a lot too. Usually it takes to form of "I tried printing it with my red PLA and it failed but everything was fine with my blue PLA".

There are many other variations on this (changing slicers for example).

Learn how to diagnose problems. This requires careful observation (#6). Once you've identified where the problem occurs (let's say getting the first layer to stick) then PRACTICE that piece (see #3) until you sort it out. No need to run through the entire process over and over. Isolate the problem, formulate a hypothesis on what you think might be happening and design a test to prove or disprove your hypothesis. If you see a problem and can't formulate a hypothesis THEN seek help! Or, pre-test your hypothesis here to get some experienced feedback. But, whatever you do, try to work through the diagnostic process yourself first, that's how you learn.

Footnote: Many years ago (20) my company had an annual laboratory safety week (I worked in a corporate R&D lab with lots of nasty stuff). One of the annual favorites was a gentleman from OSHA who talked about electrical safety. He started his presentation with a black and white video from the 1940s (I think) of a speaker walking up to a microphone on stage. The presentation was being filmed. The speaker reached up and grabbed the mic and was immediately thrown back and fell to the stage unconscious. Members of the audience rushed up to help him. This was all on video. As 4 or 5 people worked to help the victim, you see a gentleman casually walk up to the mic, reach out his hand and touch the mic. He was immediately thrown back and collapsed on the stage next to victim #1. Literally 30 seconds later a THIRD audience member walked up to the mic (now there are 2 victims on the stage and a hoard of people working to revive them) and carefully reached out his finger (looked like the scene from ET) and very, very gently touched the mic with just the tip of his finger. He was immediately thrown to the stage as the third victim. All of this was caught on video. No one died (we were told). Neither of the second two victims stopped to think about the problem, consequences or solutions.

#12 Be a Fanboy.

I am probably going to lose some fans for this post about cooling fans!

Don't think of a part cooling fan as an object. Instead, think about "air flow". If you need cooling on a PLA (or other material) part, then you need to understand air flow. Not all cooling fans are created equally. Consider this, some folks use a 40mm, some a 25mm, some (like me) a 25mm squirrel cage fan. Some are mounted to blow the full fan width stream at the nozzle area, some have a duct or some (like mine) have a very focused soda straw duct). So comments like "run your fan at 1/2 speed" are not specific enough to be useful information. Instead, you need to understand how your particular fan, it's arrangement, your material, etc, all relate to the air flow.

Firstly, using the previous strategies, try to minimize or eliminate the need for any sort of air cooling. Slowing a print down (#5) is one great way to do this. It also gives you a chance to see (#6) where any problem areas on a print might be. You can use this information to focus the right amount of air flow on the problematic areas. The tendency for many is to use as much air as possible. It is much better, more consistent, and more reliable to use as little air flow as necessary. This puts less thermal stress on the printed part.
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

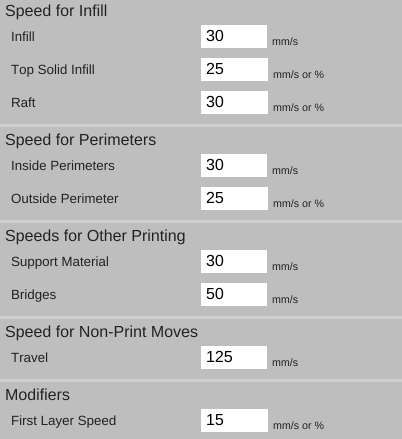
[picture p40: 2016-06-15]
User Guide/Images/speed page.png

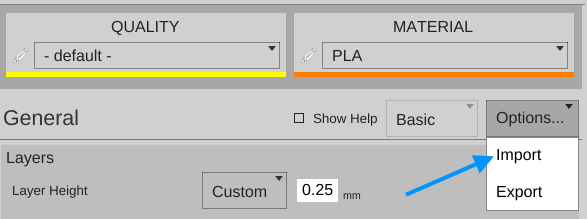
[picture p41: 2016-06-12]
User Guide/Images/import settings.png

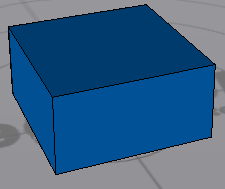
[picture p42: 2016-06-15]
User Guide/Images/outlines.png

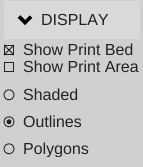
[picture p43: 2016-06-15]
User Guide/Images/display.png

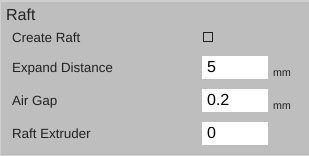
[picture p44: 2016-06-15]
User Guide/Images/raft options.png

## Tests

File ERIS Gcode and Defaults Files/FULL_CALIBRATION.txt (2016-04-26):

;  ERIS Delta Auotcalibration Script
M202 Z1850
G69 S2 ;Endstop Calibration
M117 ENDSTOPS CALIBRATED
G68 ;Horizontal Radius Calibration
M117 HORIZONTAL RADIUS CALIBRATED
G30 S2 ;Z height calibration
M117 Z Height Calibrated
M202 Z400 ;  DEFAULT ACCEL FOR TRAVLE MOVES
M500
G4 S2
M117 SAVING CALIBRATION

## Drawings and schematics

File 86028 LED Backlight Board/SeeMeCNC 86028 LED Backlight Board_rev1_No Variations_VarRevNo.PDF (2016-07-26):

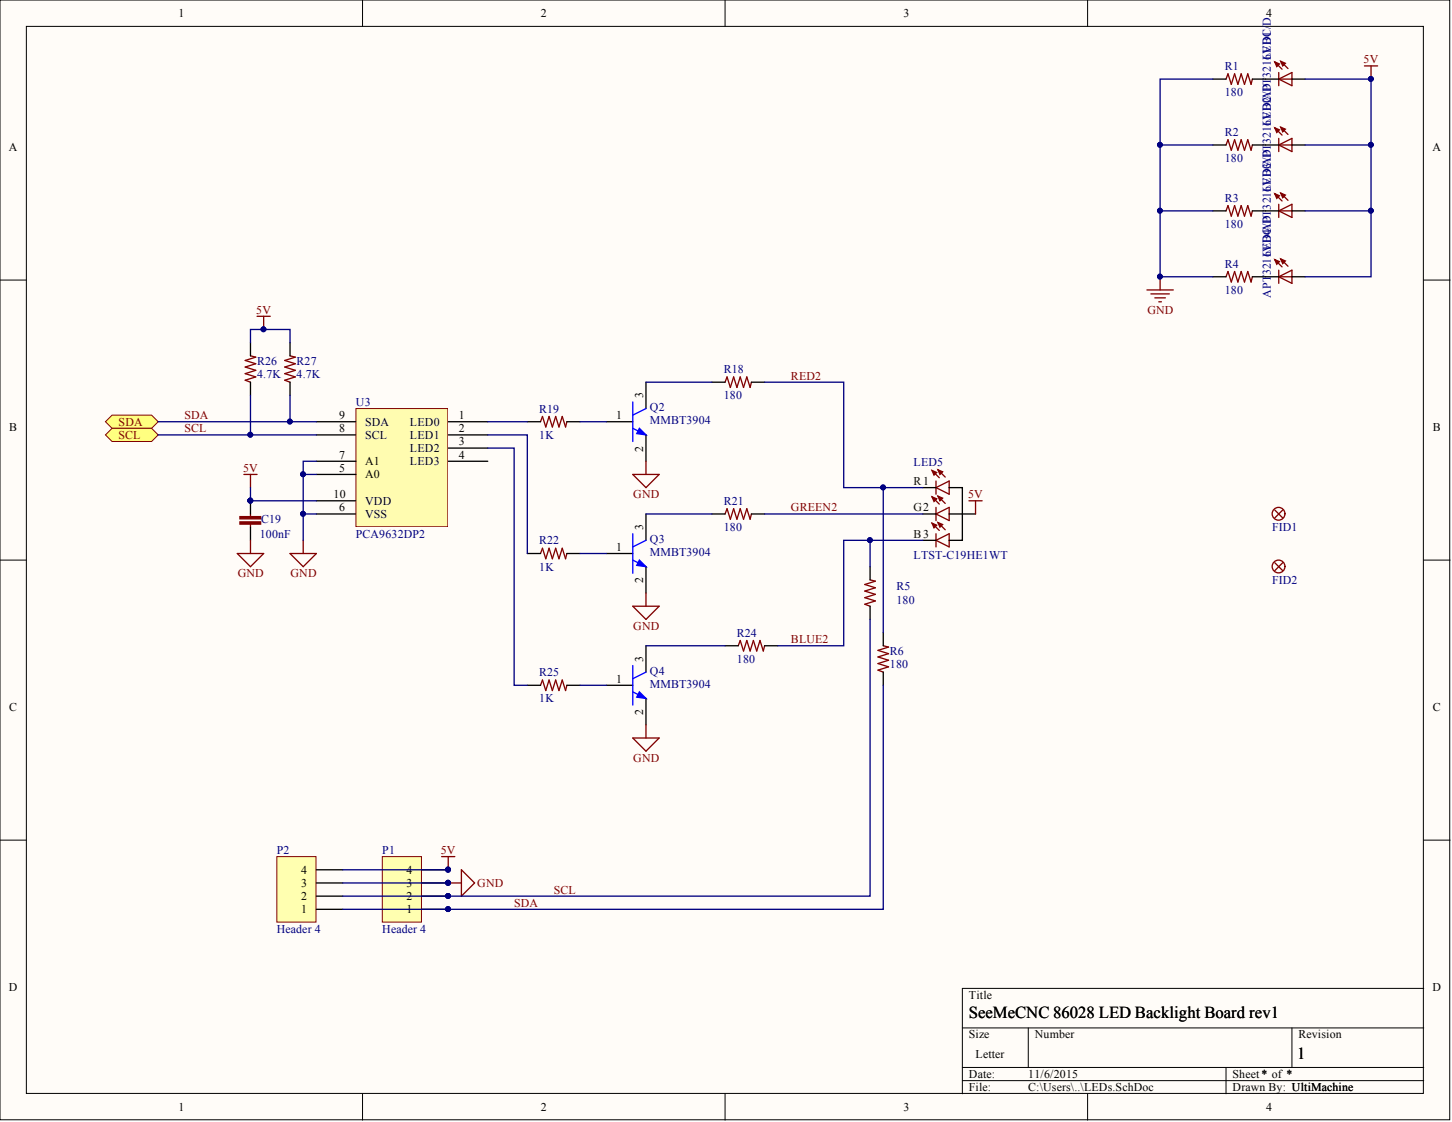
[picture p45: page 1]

1 | SDA

Title
SeeMeCNC 86028 LED Backlight Board rev1

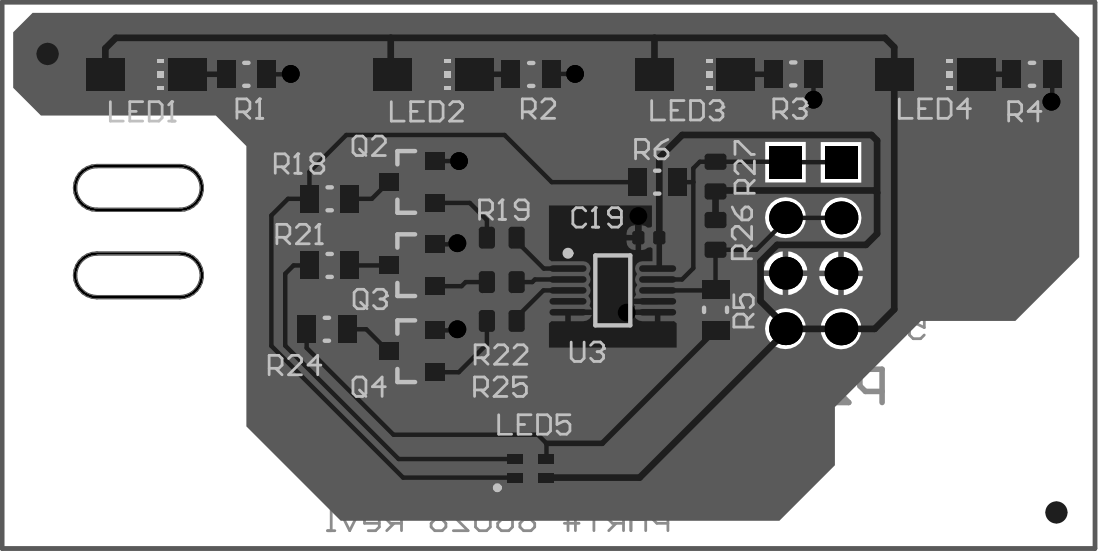
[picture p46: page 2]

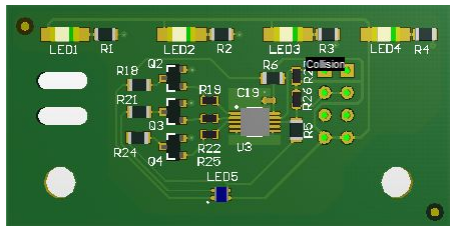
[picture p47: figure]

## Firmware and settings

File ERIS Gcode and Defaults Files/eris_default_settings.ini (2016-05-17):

avoid_crossing_perimeters = 1
bed_shape = circular
bed_size = 125,125
bed_temperature = 0
bottom_clip_amount = 0
bottom_solid_layers = 5
bridge_acceleration = 0
bridge_fan_speed = 100
bridge_flow_ratio = 1
bridge_speed = 50
brim_width = 0
build_height = 175
cancel_gcode = M104 S0\nG28
center_part_on_bed = 1
complete_objects = 0
connect_gcode = 
cool_extruder_lift = 0
print_leveling_solution = 3 Point Plane
print_leveling_method = Manual
print_leveling_required_to_print = 0
manual_probe_paper_width = .1
cooling = 1
create_raft = 0
default_acceleration = 0
disable_fan_first_layers = 2
end_gcode = M104 S0 ; turn off temperature\nG91\nG1 Z5.0 E-3.5 F12000\nG90\nG28 \nM84     ; disable motors
external_perimeter_speed = 25
external_perimeters_first = 0
extra_perimeters = 1
extruder_clearance_height = 20
extruder_clearance_radius = 20
extruder_count = 1
extruder_offset = 0x0
extruder_wipe_temperature = 0
extruders_share_temperature = 0
extrusion_axis = E
extrusion_multiplier = 1
extrusion_width = 0.6
fan_always_on = 0
fan_below_layer_time = 60
filament_diameter = 1.75
fill_angle = 0
fill_density = 10%
fill_pattern = rectilinear
first_layer_acceleration = 0
first_layer_bed_temperature = 0
first_layer_extrusion_width = 180%
first_layer_height = 0.3
first_layer_speed = 15
first_layer_temperature = 200
g0 = 0
gap_fill_speed = 30
gcode_arcs = 0
gcode_comments = 0
gcode_flavor = reprap
gcode_output_type = REPRAP
has_fan = 0
has_hardware_leveling = 1
has_heated_bed = 0
has_power_control = 0
has_sd_card_reader = 0
show_reset_connection = 1
heat_extruder_before_homing = 1
include_firmware_updater = Simple Arduino
infill_acceleration = 0
infill_every_layers = 1
infill_extruder = 1
infill_extrusion_width = 0.6
infill_first = 
infill_only_where_needed = 0
infill_overlap_perimeter = 0.08
infill_speed = 30
infill_type = TRIANGLES
layer_gcode = 
layer_height = 0.2
layer_to_pause = 
max_fan_speed = 100
min_extrusion_before_retract = 0
min_fan_speed = 100
min_print_speed = 5
min_skirt_length = 3
notes = 
nozzle_diameter = 0.5
only_retract_when_crossing_perimeters = 1
ooze_prevention = 0
output_filename_format = [input_filename_base].gcode
overhangs = 1
pause_gcode = G91\nG1 Z10 E-5.0 F12000\nG90
perimeter_acceleration = 0
perimeter_extruder = 1
perimeter_extrusion_width = 0.6
external_perimeter_extrusion_width = 100%
perimeter_speed = 30
perimeters = 3
post_process = 
print_center = 0,0
raft_air_gap = .2
raft_extruder = 0
raft_extra_distance_around_part = 5
raft_fan_speed_percent = 100
raft_layers = 0
raft_print_speed = 30
bed_remove_part_temperature = 0
randomize_start = 
repair_outlines_extensive_stitching = 1
repair_outlines_keep_open = 1
resolution = 0
resume_gcode = G91\nG1 Z-10 E5.5 F12000\nG90
retract_before_travel = 2.5
retract_layer_change = 0
retract_length = 4.5
retract_length_tool_change = 10
retract_lift = 1
retract_restart_extra = 0
retract_restart_extra_toolchange = 0
retract_when_changing_islands = 1
retract_speed = 100
skirt_distance = 3
skirt_height = 1
skirts = 2
slowdown_below_layer_time = 40
small_perimeter_speed = 30
solid_fill_pattern = rectilinear
solid_infill_below_area = 20
solid_infill_every_layers = 0
solid_infill_extrusion_width = 0.6
solid_infill_speed = 30
solid_shell = 0
spiral_vase = 0
standby_temperature_delta = -5
start_gcode = G28
start_perimeters_at_concave_points = 0
start_perimeters_at_non_overhang = 1
support_air_gap = 1
support_material = 0
support_material_angle = 0
support_material_percent = 50
support_material_create_internal_support = 0
support_material_create_perimeter = 0
support_material_enforce_layers = 0
support_material_extruder = 1
support_material_extrusion_width = 100%
support_material_infill_angle = 0
support_material_interface_extruder = 1
support_material_interface_layers = 0
support_material_interface_spacing = 0
support_material_pattern = rectilinear
support_material_spacing = 2.5
support_material_speed = 30
support_material_threshold = 40
support_material_xy_distance = 1
support_material_z_distance = 0.15
support_material_z_gap_layers = 1
support_type = GRID
temperature = 210
thin_walls = 1
threads = 4
toolchange_gcode = 
top_infill_extrusion_width = 0.6
top_solid_infill_speed = 25
top_solid_layers = 5
travel_speed = 125
use_firmware_retraction = 0
use_relative_e_distances = 0
vibration_limit = 0
wipe = 1
wipe_shield_distance = 0
wipe_tower_size = 0
z_can_be_negative = 0
z_offset = 0.2

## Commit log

2015-07-29 Pushing up init. firmware used on ERIS prototypes
    Initial push for firmware with all the autolevel configs as well as base
    for choosing printer model to make one FW to rule them all!
    [Configuration.h]
2015-07-30 CAD Files
    publish design
    [0250ID - 0625OD - 0196W.IGS, 10X2005X01W_51040681.IGS, 16109 Foot_triangle base.IGS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]
2015-11-11 Fixed default config & motor current mapping
    added array calls to commands.cpp to call motor current from
    configuration.h
    Fixed default machine type from droplit to Eris
    [Configuration.h]
2015-11-11 Updating default configs
    Updated configuration.h defaults
    [Configuration.h]
2016-03-01 added firmware
    february changes pre-production firmware
    [Configuration.h]
2016-03-01 Moved cores/libraries directories
    Moved cores/libraries directory outside main repetier folder for 1.6.X
    arduino compatibility
2016-03-01 updating firmware
    Updating defaults
    [Configuration.h]
2016-03-01 Updated defaults for motor current etc...
    Updated motor current defaults. Moved motor current into
    configuration.h and fixed commands.cpp so motor currents were being
    obeyed for mini-rambo. Test printing now with new values
    [Configuration.h]
2016-03-04 update defaults
    update accel/jerk defaults for eris
    [Configuration.h]
2016-03-04 Added UltiMachine firmware for accel probing
    Added firmware DIR from ultimachine for accel probing testing
    [0250ID - 0625OD - 0196W.IGS, 10X2005X01W_51040681.IGS, 16109 Foot_triangle base.IGS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]
2016-03-04 added pins for case/HE fans
    Added readme description to remind me to re-map pins for case fan and HE
    fans
2016-03-07 updating FW and config. fans
    setup fan pins and configuration for prototype2
    [Configuration.h]
2016-03-07 updated printer radius
    updated printer radius settings
    [Configuration.h]
2016-03-07 minor default updates
    update defaults on prototype
    [Configuration.h]
2016-03-08 updating probe settings
    updating probe defines and defaults etc...
    [Configuration.h]
2016-03-08 probe tweaks
    working on probe settings
    [Configuration.h]
2016-03-08 working config defaults
    Added results from probe test and gcode for calibrating eris
    [Configuration.h]
2016-03-08 renamed old firmware folder
    renamed old firmware folder and updated sensitivity of probe default to
    25
    [Configuration.h]
2016-03-10 updated defaults
    updated defaults
    [Configuration.h]
2016-03-11 False trigger re-tap
    Set firmware defaults on calibration G-Codes before running
    G30 center tap z-height calibration
    Double tap each point to detect false triggers if both taps are not
    within .1mm of each other.
    [Configuration.h]
2016-03-16 Error Checks
    Eris LCD support pinned for red board LCD
    Safety check for probe, after 5 fails, outputs error to terminal and
    stops probing.
    Set default probe height from 15 to 7 and speed from 50 to 60
    [Configuration.h]
2016-03-16 modified defaults and commented out G30 S wierdo
    [Configuration.h]
2016-03-16 defaults updated
    default
    [Configuration.h]
2016-04-01 updated defautls
    Found that probing with speed 90 was WAY more consistent.
    MAKE SURE that the probe start script in mattercontrol/gcode/etc...
    executes M202 Z1850 at start and M202 Z400 at end to up the accel value
    for probing
    [Configuration.h]
2016-04-01 Added Calibration gcode
    Added gcode for macros/scripts/calibration
2016-04-04 updated defaults and reset probe startup script
    fixed probe startup script and updated defaults
    [Configuration.h]
2016-04-04 Updated calibration gcode text
    Updated calibration gcode file
2016-04-04 disabled bed checking for firmware
    disabled the heated bed ( set to 0 )
    [Configuration.h]
2016-04-11 UPDATED extrude max length
    updated extrude length so we can add the filament change to the menus
    [Configuration.h]
2016-04-26 Added Gcode files for ERIS
    Added probing Gcode. Added Filament load and unload Gcode files too!
2016-04-26 added probing and filament gcode
    added probing and filament gcode files to probe, load and unload
    filaments
2016-05-05 updated commands.cpp to error out and retry
    pulled in andy's commands.cpp code
    [Configuration.h]
2016-05-05 Updated hotend configs
    updated hotend configs and set therm table for 104GT2 semitec based on
    datasheets
    [Configuration.h]
2016-05-05 Update thermistor beta value
    Updated to 4450 beta value
    [Configuration.h]
2016-05-06 Removed old Firmware folder and added default slicing settings
    Removed old firmware and added slice defaults and other gcode files
    [Configuration.h]
2016-05-16 Updated extruder motor current
    Updated motor current for extruder
    [Configuration.h]
2016-05-17 Updated defaults and adjusted motor current
    Updated default slice settings and also updated motor current to a
    slightly lower value. This allows the extruder more torque but not so
    much that it grinds off filament.
    [Configuration.h]
2016-06-08 Update Configuration.h to integrate all printers settings into one
    added ifdefs to identify and set parameters for all printer based on
    printer model for hotend, probing etc...
    [Configuration.h]
2016-06-08 renamed files
    renamed files
    [Configuration.h]
2016-07-26 Added 86028 LED backlight board
    Added 86028 LED backlight board
    [SeeMeCNC 86028 LED Backlight Board_Rev2.GBL, SeeMeCNC 86028 LED Backlight Board_Rev2.GBO, SeeMeCNC 86028 LED Backlight Board_Rev2.GBP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]
2017-01-27 Updated calibration instructions to new process.
